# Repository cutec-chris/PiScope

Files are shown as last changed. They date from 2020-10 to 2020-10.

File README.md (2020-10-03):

# PiScope V3
PiScope is an small mobile Telescope for Astro and Nature Photography its designed to be as Mobile as Possible and can be driven with an Powerbank

PiScope, Mini Telescope for different lenses

The Step Resolution of the mechanic is:

Vertikal GradperStep:0.0703125<br>
Horizontal GradperStep:0.074800532<br>

## Lenses

[OH1](construction/OH1.md) - Lens holder for small C-Mount lenses like original raspberry Pi Lenses<br>
[OH2](construction/OH2.md) - Lens holder for Vivitar 70-200mm Cannon FD Tele Lens<br>
[OH3](construction/OH3.md) - Lens holder for Waveshare 8-50mm C-Mount Lens<br>
[OH4](construction/OH4.md) - Lens holder for Tokina 500mm FD Mount Lens<br>

## Electronics
The electronics consists of an [Raspberry Pi](https://www.raspberrypi.org/) and the [HAT PCB](electronic/HAT/README.md) wich contains Motor Drivers, and Compass

## Prices

Position           | Quantity | Price | Full
------------------ | -------- | ---- | -----
3D printed Parts | 1 | ~5$ | 5$
Raspberry Pi 3 | 1 | ~ 35$ | 35$
28BYJ-48 | 2 | ~3$ | 6$
Bearing 13mm | 2 | 0.4$ | 0.8$
Raspberry Pi HQ Camera | 1 | 53$ | 53$
[HAT PCB](electronic/HAT/README.md#BOM) | 1 | 6.5$ | 6.5$
| | | | 106.3$

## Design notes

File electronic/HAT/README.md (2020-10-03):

This is an Motor Driver Board created for the [PiScope](https://github.com/cutec-chris/PiScope). 

It contains:
* 4 Motor Drivers wich can be used with ULN2003 or alternte DRV8825. The ULN2003 can be used with 28BYJ-48 and DEV8825 with NEMAxx<br> 
* Compass Module suppport for HMC5883L:<br>
* 4 Endswitches: <br>

## BOM

Position           | Quantity | Price | Full
------------------ | -------- | ---- | -----
PCB | 1 | ~3$ | 3$
ULN2003A | 3 | ~ 0.3$ | 0.9$
JST Pinheader | 3 | ~0.2$ | 0.6$
PI Header | 1 | ~2$ | 2$
| | | | 6.5$

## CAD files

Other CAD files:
construction/OH4_Tokina500mm.FCStd
construction/Teleskop_OH2.FCStd
construction/Base.FCStd
construction/USBCam.FCStd
construction/RaspberryPiHQCamera.FCStd
construction/RaspberryPi3.FCStd
construction/OH1_RpiHQCam.FCStd
construction/OH2_Cannon200mm.FCStd
construction/HalterBalkon.FCStd
construction/NEMA17_S.FCStd
construction/Schraube.FCStd
construction/OH3_Waveshare.FCStd

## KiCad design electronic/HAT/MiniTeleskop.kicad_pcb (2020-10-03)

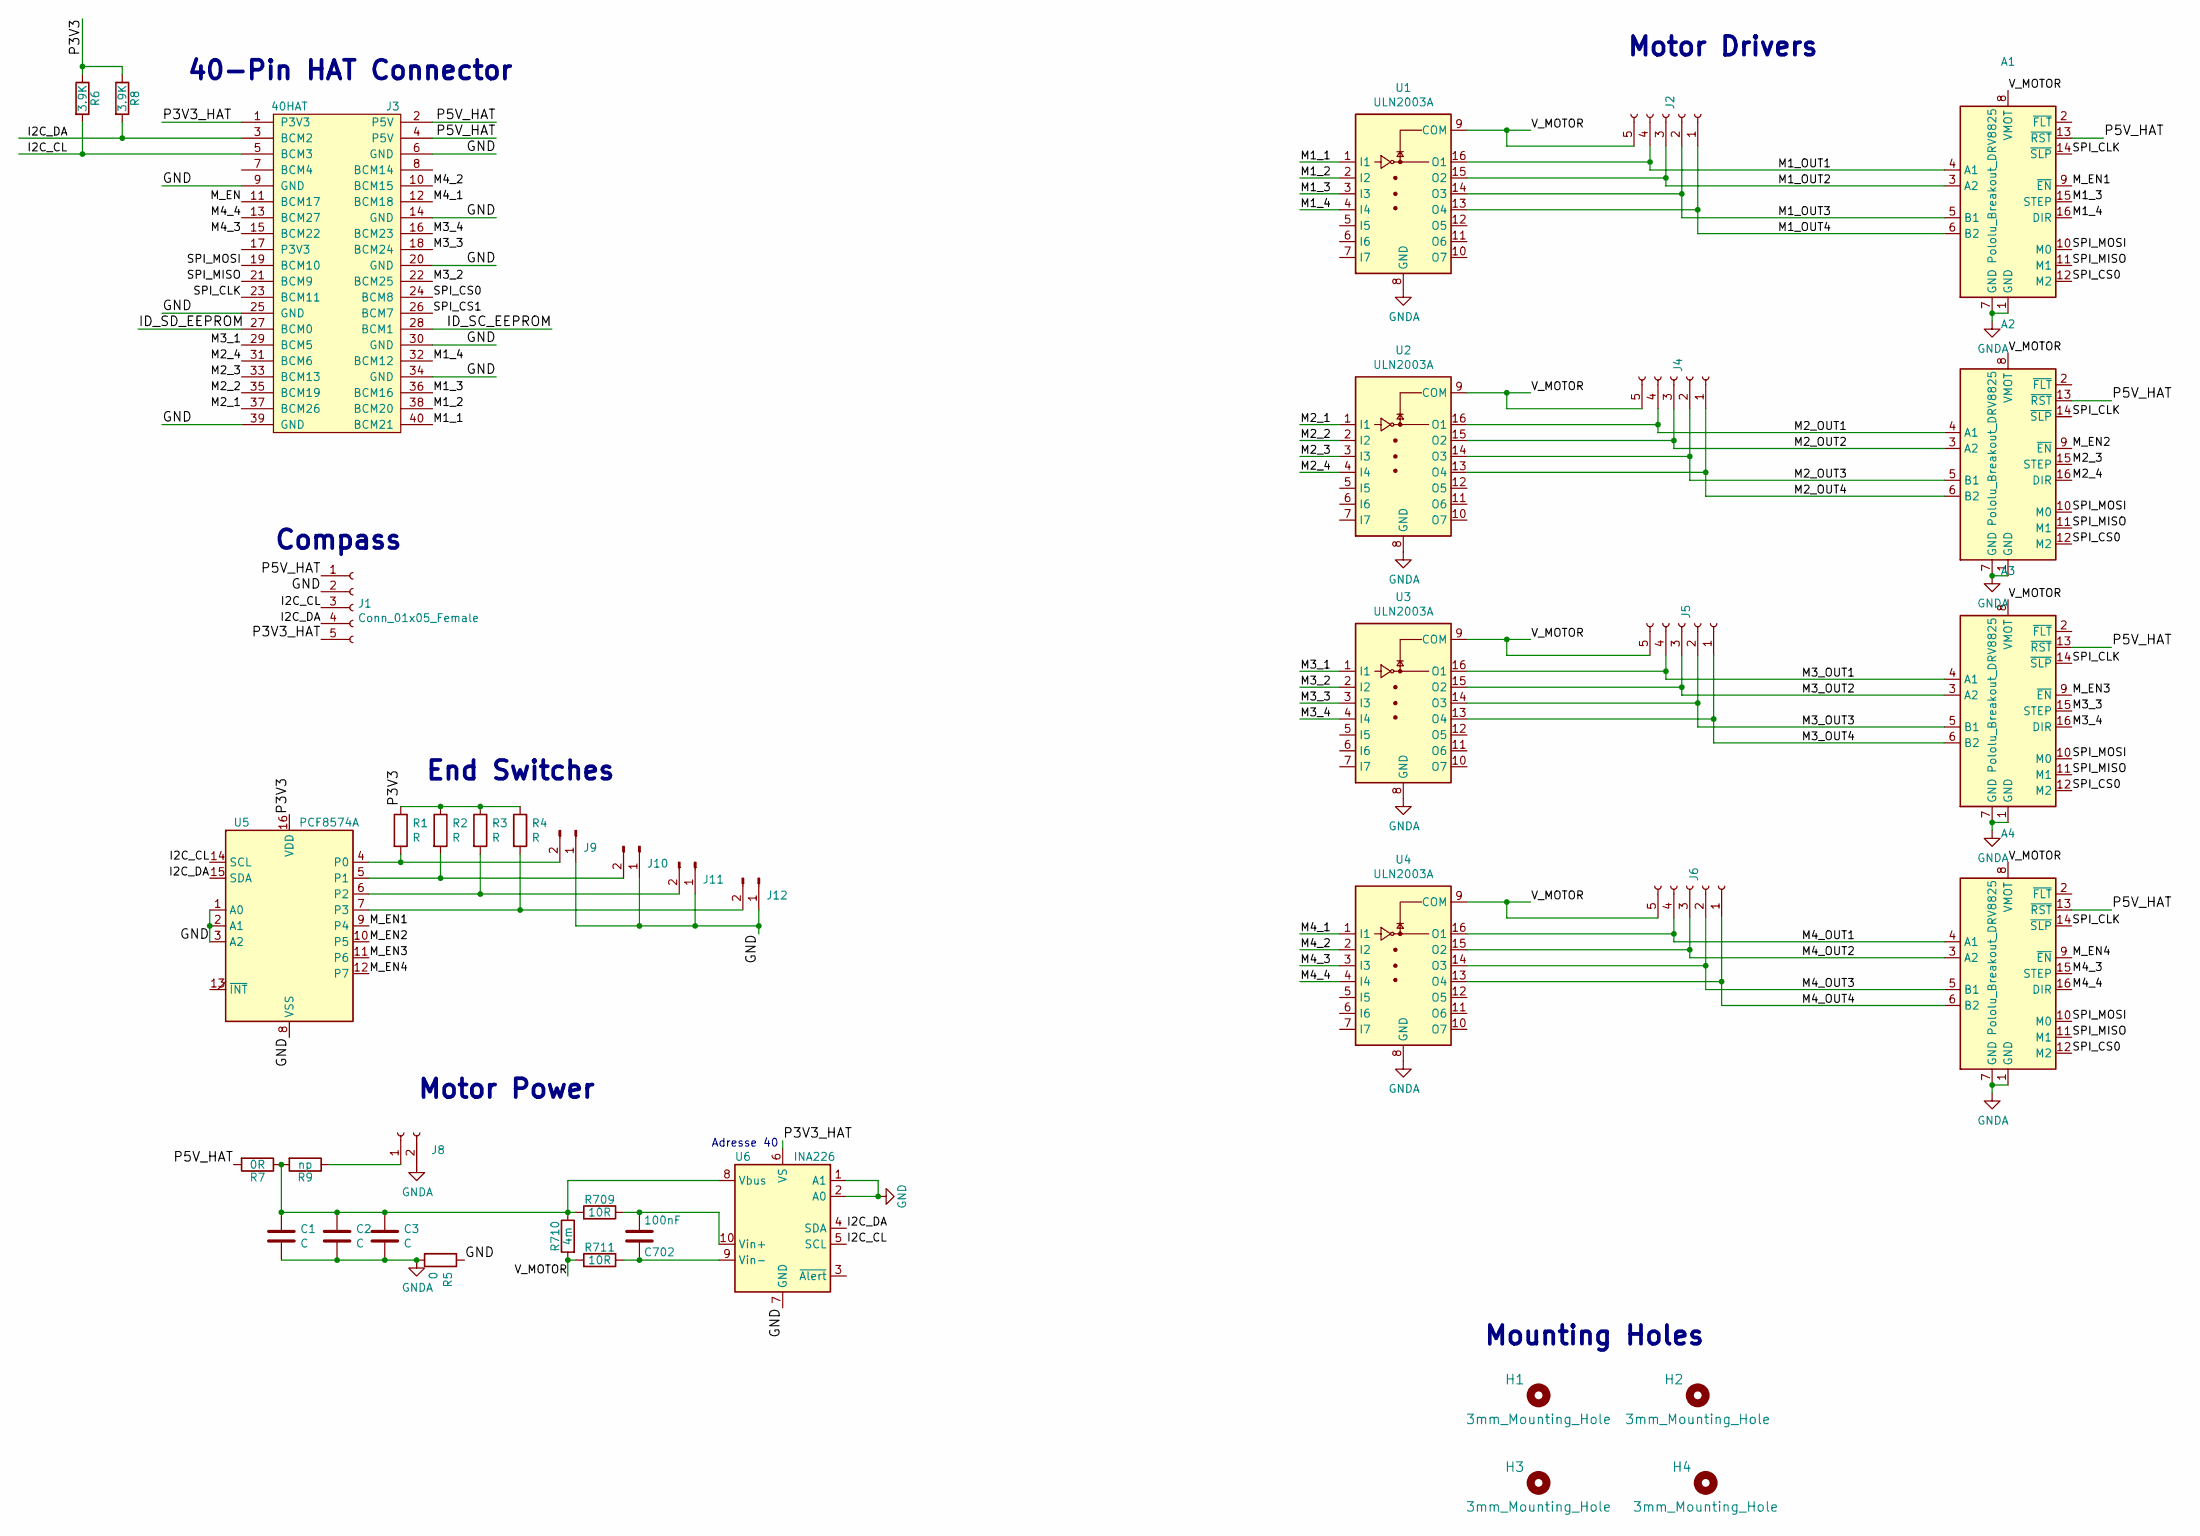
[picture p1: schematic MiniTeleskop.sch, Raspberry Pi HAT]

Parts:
A1, A2, A3, A4: Pololu_Breakout_DRV8825; Pololu_Breakout-16_15.2x20.3mm
C1, C2, C3: C; C_1206_3216Metric_Pad1.42x1.75mm_HandSolder
C702: 100nF; C_0805_2012Metric
H1, H2, H3, H4: 3mm_Mounting_Hole; NPTH_3mm_ID
J1: Conn_01x05_Female; PinHeader_1x05_P2.54mm_Vertical
J2, J4, J5, J6: Conn_01x05_Female; JST_XH_B5B-XH-A_1x05_P2.50mm_Vertical
J3: 40HAT; PinSocket_2x20_P2.54mm_Vertical
J8: Conn_01x02_Female; JST_NV_B02P-NV_1x02_P5.00mm_Vertical
J9, J10, J11, J12: Conn_01x02_Male; PinHeader_1x02_P2.54mm_Vertical
R1, R2, R3, R4: R; R_0805_2012Metric_Pad1.15x1.40mm_HandSolder
R5: 0; R_0805_2012Metric_Pad1.15x1.40mm_HandSolder
R6, R8: 3.9K; R_0805_2012Metric_Pad1.15x1.40mm_HandSolder
R7: 0R; R_0805_2012Metric_Pad1.15x1.40mm_HandSolder
R9: np; R_0805_2012Metric_Pad1.15x1.40mm_HandSolder
R709, R711: 10R; R_0805_2012Metric
R710: 4m; R_2512_6332Metric
U1, U2, U3, U4: ULN2003A; SOIC-16_3.9x9.9mm_P1.27mm
U5: PCF8574A; SOIC-16W_7.5x10.3mm_P1.27mm
U6: INA226; VSSOP-10_3x3mm_P0.5mm

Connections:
/I2C_CL: J1.3, J3.5 (BCM3), R6.2, U5.14 (SCL), U6.5 (SCL)
/I2C_DA: J1.4, J3.3 (BCM2), R8.2, U5.15 (SDA), U6.4 (SDA)
/ID_SC_EEPROM: J3.28 (BCM1)
/ID_SD_EEPROM: J3.27 (BCM0)
/M1_1: J3.40 (BCM21), U1.1 (I1)
/M1_2: J3.38 (BCM20), U1.2 (I2)
/M1_3: A1.15 (STEP), J3.36 (BCM16), U1.3 (I3)
/M1_4: A1.16 (DIR), J3.32 (BCM12), U1.4 (I4)
/M1_OUT1: A1.4 (A1), J2.4, U1.16 (O1)
/M1_OUT2: A1.3 (A2), J2.3, U1.15 (O2)
/M1_OUT3: A1.5 (B1), J2.2, U1.14 (O3)
/M1_OUT4: A1.6 (B2), J2.1, U1.13 (O4)
/M2_1: J3.37 (BCM26), U2.1 (I1)
/M2_2: J3.35 (BCM19), U2.2 (I2)
/M2_3: A2.15 (STEP), J3.33 (BCM13), U2.3 (I3)
/M2_4: A2.16 (DIR), J3.31 (BCM6), U2.4 (I4)
/M2_OUT1: A2.4 (A1), J4.4, U2.16 (O1)
/M2_OUT2: A2.3 (A2), J4.3, U2.15 (O2)
/M2_OUT3: A2.5 (B1), J4.2, U2.14 (O3)
/M2_OUT4: A2.6 (B2), J4.1, U2.13 (O4)
/M3_1: J3.29 (BCM5), U3.1 (I1)
/M3_2: J3.22 (BCM25), U3.2 (I2)
/M3_3: A3.15 (STEP), J3.18 (BCM24), U3.3 (I3)
/M3_4: A3.16 (DIR), J3.16 (BCM23), U3.4 (I4)
/M3_OUT1: A3.4 (A1), J5.4, U3.16 (O1)
/M3_OUT2: A3.3 (A2), J5.3, U3.15 (O2)
/M3_OUT3: A3.5 (B1), J5.2, U3.14 (O3)
/M3_OUT4: A3.6 (B2), J5.1, U3.13 (O4)
/M4_1: J3.12 (BCM18), U4.1 (I1)
/M4_2: J3.10 (BCM15), U4.2 (I2)
/M4_3: A4.15 (STEP), J3.15 (BCM22), U4.3 (I3)
/M4_4: A4.16 (DIR), J3.13 (BCM27), U4.4 (I4)
/M4_OUT1: A4.4 (A1), J6.4, U4.16 (O1)
/M4_OUT2: A4.3 (A2), J6.3, U4.15 (O2)
/M4_OUT3: A4.5 (B1), J6.2, U4.14 (O3)
/M4_OUT4: A4.6 (B2), J6.1, U4.13 (O4)
/M_EN: J3.11 (BCM17)
/M_EN1: A1.9 (~EN), U5.9 (P4)
/M_EN2: A2.9 (~EN), U5.10 (P5)
/M_EN3: A3.9 (~EN), U5.11 (P6)
/M_EN4: A4.9 (~EN), U5.12 (P7)
/P3V3: R1.1, R2.1, R3.1, R4.1, R6.1, R8.1, U5.16 (VDD)
/P3V3_HAT: J1.5, J3.1 (P3V3), U6.6 (VS)
/P5V_HAT: A1.13 (~RST), A2.13 (~RST), A3.13 (~RST), A4.13 (~RST), J1.1, J3.2 (P5V), J3.4 (P5V), R7.2
/SPI_CLK: A1.14 (~SLP), A2.14 (~SLP), A3.14 (~SLP), A4.14 (~SLP), J3.23 (BCM11)
/SPI_CS0: A1.12 (M2), A2.12 (M2), A3.12 (M2), A4.12 (M2), J3.24 (BCM8)
/SPI_CS1: J3.26 (BCM7)
/SPI_MISO: A1.11 (M1), A2.11 (M1), A3.11 (M1), A4.11 (M1), J3.21 (BCM9)
/SPI_MOSI: A1.10 (M0), A2.10 (M0), A3.10 (M0), A4.10 (M0), J3.19 (BCM10)
/V_MOTOR: A1.8 (VMOT), A2.8 (VMOT), A3.8 (VMOT), A4.8 (VMOT), J2.5, J4.5, J5.5, J6.5, R710.2, R711.2, U1.9 (COM), U2.9 (COM), U3.9 (COM), U4.9 (COM)
GND: J1.2, J3.6 (GND), J3.9 (GND), J3.14 (GND), J3.20 (GND), J3.25 (GND), J3.30 (GND), J3.34 (GND), J3.39 (GND), J9.1, J10.1, J11.1, J12.1, R5.1, U5.1 (A0), U5.2 (A1), U5.3 (A2), U5.8 (VSS), U6.1 (A1), U6.2 (A0), U6.7 (GND)
GNDA: A1.1 (GND), A1.7 (GND), A2.1 (GND), A2.7 (GND), A3.1 (GND), A3.7 (GND), A4.1 (GND), A4.7 (GND), C1.2, C2.2, C3.2, J8.2, R5.2, U1.8 (GND), U2.8 (GND), U3.8 (GND), U4.8 (GND)
unnamed: C1.1, C2.1, C3.1, R7.1, R9.2, R709.2, R710.1, U6.8 (Vbus)
unnamed: C702.1, R711.1, U6.9 (Vin-)
unnamed: C702.2, R709.1, U6.10 (Vin+)
unnamed: J8.1, R9.1
unnamed: J9.2, R1.2, U5.4 (P0)
unnamed: J10.2, R2.2, U5.5 (P1)
unnamed: J11.2, R3.2, U5.6 (P2)
unnamed: J12.2, R4.2, U5.7 (P3)

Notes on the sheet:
Mounting Holes
40-Pin HAT Connector
Adresse 40
Motor Power
Motor Drivers
End Switches
Compass

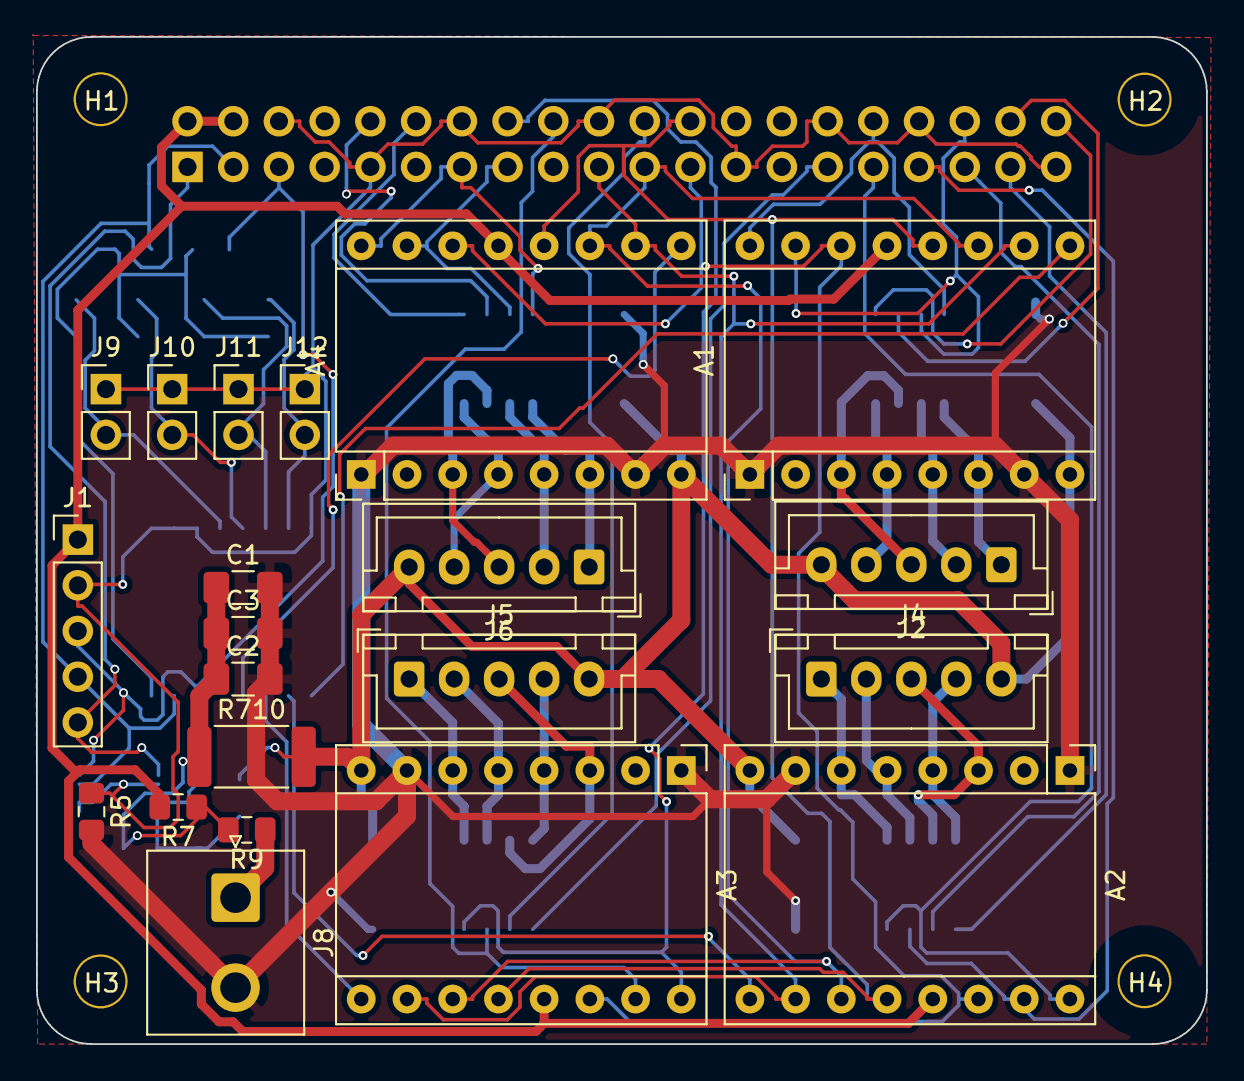
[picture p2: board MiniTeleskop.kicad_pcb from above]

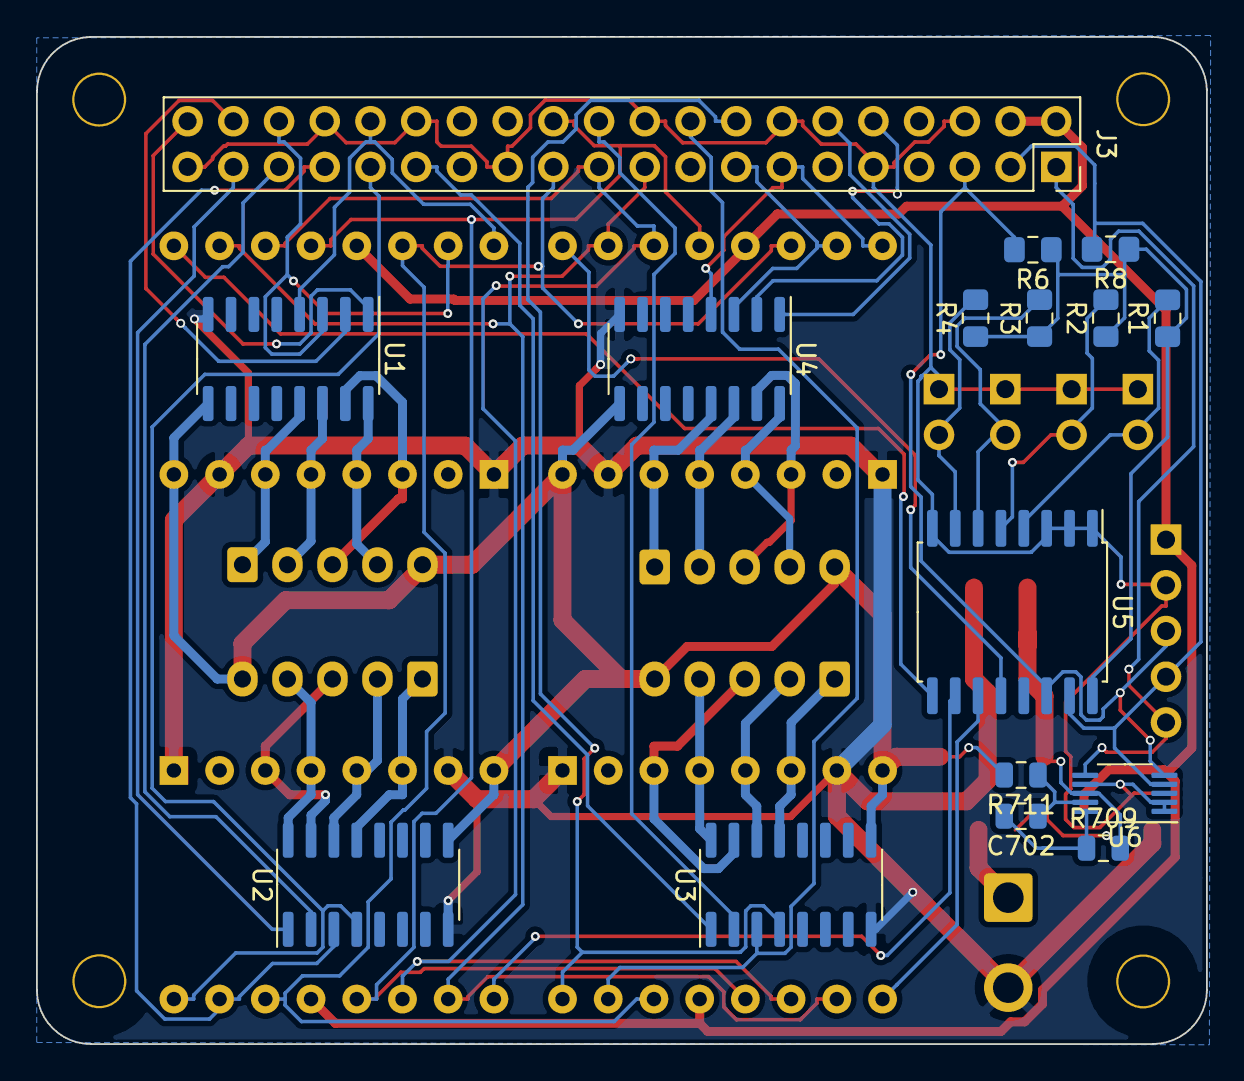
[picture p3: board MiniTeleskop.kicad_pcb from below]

Board: 2 copper layers, 65.0 x 56.0 mm, 41 parts (16 on the bottom side), 56 nets.

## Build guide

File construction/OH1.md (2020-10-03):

Holder for Raspi HQ Camera and small Lenses

This Lens Holder holds just the Raspi HQ Camera, so its able to hold any small Lens attachable to C(S)-Mount

## BOM

Position           | Quantity | Price | Full
------------------ | -------- | ---- | -----
3D printed Parts | 1 | ~1$ | 1$
Screw | 1 | ~1$ | 1$
| | | | 2$

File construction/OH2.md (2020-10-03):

Holder for Raspi HQ Camera and Vivitar 70-200mm Telelens

## BOM

Position           | Quantity | Price | Full
------------------ | -------- | ---- | -----
3D printed Parts | 1 | ~1$ | 1$
Screw | 1 | ~1$ | 1$
Lens | 1 | ~35$ | 35$
28BYJ-48 | 1 | ~3$ | 3$
Bearing 13mm | 4 | 0.8$ | 0.8$
| | | | 39.8$

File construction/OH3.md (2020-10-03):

Holder for Raspi HQ Camera and Waveshare 8-50mm Lens

## BOM

Position           | Quantity | Price | Full
------------------ | -------- | ---- | -----
3D printed Parts | 1 | ~1$ | 1$
Screw | 1 | ~1$ | 1$
Lens | 1 | ~35$ | 35$
28BYJ-48 | 2 | ~3$ | 6$
| | | | 42$

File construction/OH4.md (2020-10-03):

Holder for Tokina 500mm Lens

## BOM

Position           | Quantity | Price | Full
------------------ | -------- | ---- | -----
3D printed Parts | 1 | ~2$ | 2$
Screw | 1 | ~1$ | 1$
Lens | 1 | ~65$ | 65$
28BYJ-48 | 1 | ~3$ | 3$
| | | | 71$

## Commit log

2020-10-03 Initial Move from private Repo
    [Base.FCStd, HalterBalkon.FCStd, MiniTeleskop.kicad_pcb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]
2020-10-03 Add Tokina 500mm lensholder
    [OH4_Tokina500mm.FCStd]
2020-10-03 First Useable Version of Tokina Holder?
    [OH4_Tokina500mm.FCStd]
2020-10-08 Add USB Camera
    [USBCam.FCStd]
2020-10-08 Add USB camera to Base
    [Base.FCStd, OH4_Tokina500mm.FCStd, Teleskop_OH2.FCStd]
